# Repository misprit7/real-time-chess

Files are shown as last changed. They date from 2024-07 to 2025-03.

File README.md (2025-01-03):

<h1 align="center">
  <!--<picture><img src="./doc/img/logo.png" height="400"/></picture>-->
  <br />
  Real Time Chess
</h1>
<h2 align="center">
  A physical chess board without the concept of turns
</h2>
<h2 align="center">
  Video explanation: https://youtu.be/y7VtSK23_Jg
</h2>

# Pitch

Chess is boring. I'm boring too so I enjoy it anyways, but I can't help but think "I could design it better." Normally in chess players move sequentially in turns, but this introduces a huge latency bug that the developers of chess forgot to patch: you spend literally half the time waiting for your opponent!

The obvious solution is just get rid of the concept of turns in chess altogether and let players move whenever they want. Real time strategy games like StarCraft and Age of Empires are much more fun and spectator friendly than chess, so this should be a pretty uncontroversial minor rules update that can be implemented before the next world championship. To prevent things from getting too chaotic over the board each piece has an individual cooldown, so once it's been moved it can't move for a fixed period afterwards.

However there's an unfortunate roadblock to the widespread adoption of real time chess: as the [Niemann controversy](https://www.cnn.com/2023/09/26/sport/hans-niemann-denies-sex-toys-cheating-chess-spt-intl/index.html) has made all too clear, chess is [not immune](https://www.youtube.com/watch?v=QNuu8KTUEwU) from accusations of cheating through spectator **ass**istance or outside **anal**isys tools. Trying to have players self enforce these piece cooldowns is impossible. However where the intrinsic goodness of the human psyche fails, engineering is always ready to step in. This project is a physical chess board that keeps track and displays the cooldown remaining for each piece, and even physically holds them in place so no accidental cheating can occur.

# Design Files

The firmware and pcb kicad files are in this repo. For the physical design, see [the design on OnShape](https://cad.onshape.com/documents/ad9a4c8f8eed1cb460895551/w/e793072796f18b5ae284597f/e/b7ae406cfa566c5c0e6fed4b). Other than those parts that were cnced, here were the off the shelf components used:

- [Insulating washers](https://www.mcmaster.com/catalog/130/3683/95225A340): One under each electromagnet, to keep them isolated from the casing
- [Plastic screws](https://www.mcmaster.com/catalog/130/3446/92492A728): To attach electromagnets to base, plastic to prevent electrical connection
- [These](https://www.mcmaster.com/catalog/130/3435/92095A182) and [these](https://www.mcmaster.com/catalog/130/3435/92095A177) screws: to attach the internal supports and squares respectively
- [Spacers](https://www.mcmaster.com/catalog/94669A095): For an offset between the decorative and functional pcbs
- [Electromagnets](https://www.adafruit.com/product/3873): Most expensive part other than the machining, ~$600 per board. Could probably get them cheaper from China or something but for low quantities this was easiest

# Known Issues

- Power distribution: Traces on the pcbs are way undersized given there are many amps running through them, so there are large voltage drops when many pieces are on cooldown simultaneously. To solve this these traces should be much wider
- Tolerances: The pcbs have extremely tight tolerances which makes assmbling the board extremely annoying. The edges and holes should probably have more room
- Pin heights: The height of the pins for the banana connectors are taller than the mechanical design allows for, these are fairly easy to shorten using a dremel but probably something that should be fixed
- Corner screws: Given the order of assembly, it's impossible to insert/fasten the 4 corner screws

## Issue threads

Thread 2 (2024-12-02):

Parts list/Instructions

americoperez49, 2024-12-02:
Hey From Scratch,

Just came across your video for this. Looks super fun!

Would you be able to provide a complete parts list with links to where we could buy/manufacture the parts from?

Also a tutorial for how to build/assemble this would also be super helpful.

Thank you!

androng, 2024-12-03:
How much does one build cost?

Jannis-L, 2024-12-06:
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

A bill of materials can be found in the "releases", however the used electric magnets are not listed there. A google search resulted in all sorts of different versions that would fit the PCB design.
Additionally, there are no CAD-Files for the milled plates.

However, it seems like the project isn't ready for being copied, as the PCB is very much in a prototype state:
- screws that can short traces
- unoptimzed layout
- edges could be smaller
- not splitting the PCB in 4 parts would make it cheaper (only one controller needed) and easier to assemble. (I understand that it made sense for the first prototype)
- Having a small display with two buttons would allow for a ton of different online-only chess-variants to be played on it.
- The all-metal construction makes the project to expensive and hard to rebuild.
- In the video the board seems to be unreliable at detecting a piece being placed on a field and/or pulling it in place correctly.

The question on my mind: Is @misprit7 willing to maintain and update the project (or at least manage pull requests) to get it to a state where everyone can build their own version for a few hundred dollars or should we do a public fork and try to develop it further ourselves?

Sooly890, 2024-12-07:
Yes... please a guide would be useful

misprit7, 2024-12-08:
I added a link to the onshape mechanical files and the other parts I used in the readme. I won't be providing a guide, although I think most parts are reasonably self explanatory. If anyone does actually try to build one and runs into any issues with the files let me know any specific questions and I'd be happy to help.

As for cost, I'd probably expect at least $2500 for the first board. ~$700 for the electromagnets, ~$1000 for the cnced parts, ~$100 for the pieces, ~$300 for pcbs+components, plus a couple hundred for fasteners/materials/misc.

danaedf, 2024-12-10:
Interesting project!

If you make a new board revision, I would recommend increasing the layer count to 4 for dedicated GND/PWR layers. This should help with the voltage drops you have noticed when multiple pieces are on cooldown. Of course, you may decide against this, depending on the price, but as you mentionned in your readme, the 5V traces would need to be much larger if you keep it at 2 layers.

Also, decoupling capacitors near the electromagnets might be nice, because the in-rush current could drop the bus voltage enough to reset nearby LEDs. On the other hand, a high enough LED refresh rate might make this potential flicker unnoticeable. Adding footprints (even if you decide to not install them) for ceramic capacitors of 0.1uF for each LED and a 10uF near the eletromagnet's 5V would give you options if you notice issues.

misprit7, 2024-12-20:
@danaedf Yes you're totally right gnd/pwr planes are better for this, I remember regretting not putting them in but forgot to mention it when I wrote the last message. As for capacitors I haven't had any issues, although definitely something I was a bit worried about and would be reasonable to add.

Tomillium, 2025-02-06:
hey, could you provide a file with the pcb design.
-thanks

Tomillium, 2025-02-11:
Hey, I was wondering if the LEDs came on the pcb or not.
also if they don't which ones did you use?

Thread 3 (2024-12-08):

Improvement Suggestions

covenator, 2024-12-08:
Feature Suggestions for Improved Real-Time Chess Board Experience

1. Improved LED Lighting Appearance

Issue: The current LED lights that indicate board locations are not diffused, leading to a harsh and direct light output. Additionally, the LEDs are placed in a circular arrangement around the chess pieces but remain perfectly vertical.

Suggestions:

Add a diffusion layer or cover on top of the LEDs to soften the light, creating a cleaner and more professional appearance.

Slightly tilt the LEDs inward toward the chess piece. This ensures that the light focuses on the piece itself, enhancing visibility and aesthetics. The light will illuminate the chess piece better and make the overall look of the board more visually appealing.

---

2. Smart LED Highlighting for Legal Moves

Feature Request: Utilize the smart setup to enhance gameplay by displaying legal moves for a selected piece.

Details:

When a player picks up a chess piece, the LEDs (or an additional set of LEDs) light up to show all possible legal moves for that piece, similar to the way online chess platforms function.

Benefit: This feature makes it much easier for beginners to understand the game and reduces the learning curve, improving accessibility for all skill levels.

---

3. Visual Win Probability Display

Feature Request: Add a dynamic, visually engaging indicator that shows which player has a higher chance of winning based on the current board state.

Details:

Instead of displaying raw percentages, use a bar-style visual indicator that dynamically reflects the win probability.

The bar can be divided into two sections, each representing a player’s color. As the game progresses, the colors will expand or shrink, edging out the other player’s section based on who is currently leading.

The visual representation would resemble the win bars seen in classic fighting games like Street Fighter 2, where one color overtakes the other as the advantage shifts.

Example: If Player A is winning, their section of the bar will grow and dominate the other player's color, making the progression clear at a glance.

Benefit: This feature adds a fun and competitive element to the game, providing an intuitive and visually appealing way for players and spectators to track momentum shifts without relying on percentages alone.

Closed 2024-12-08.

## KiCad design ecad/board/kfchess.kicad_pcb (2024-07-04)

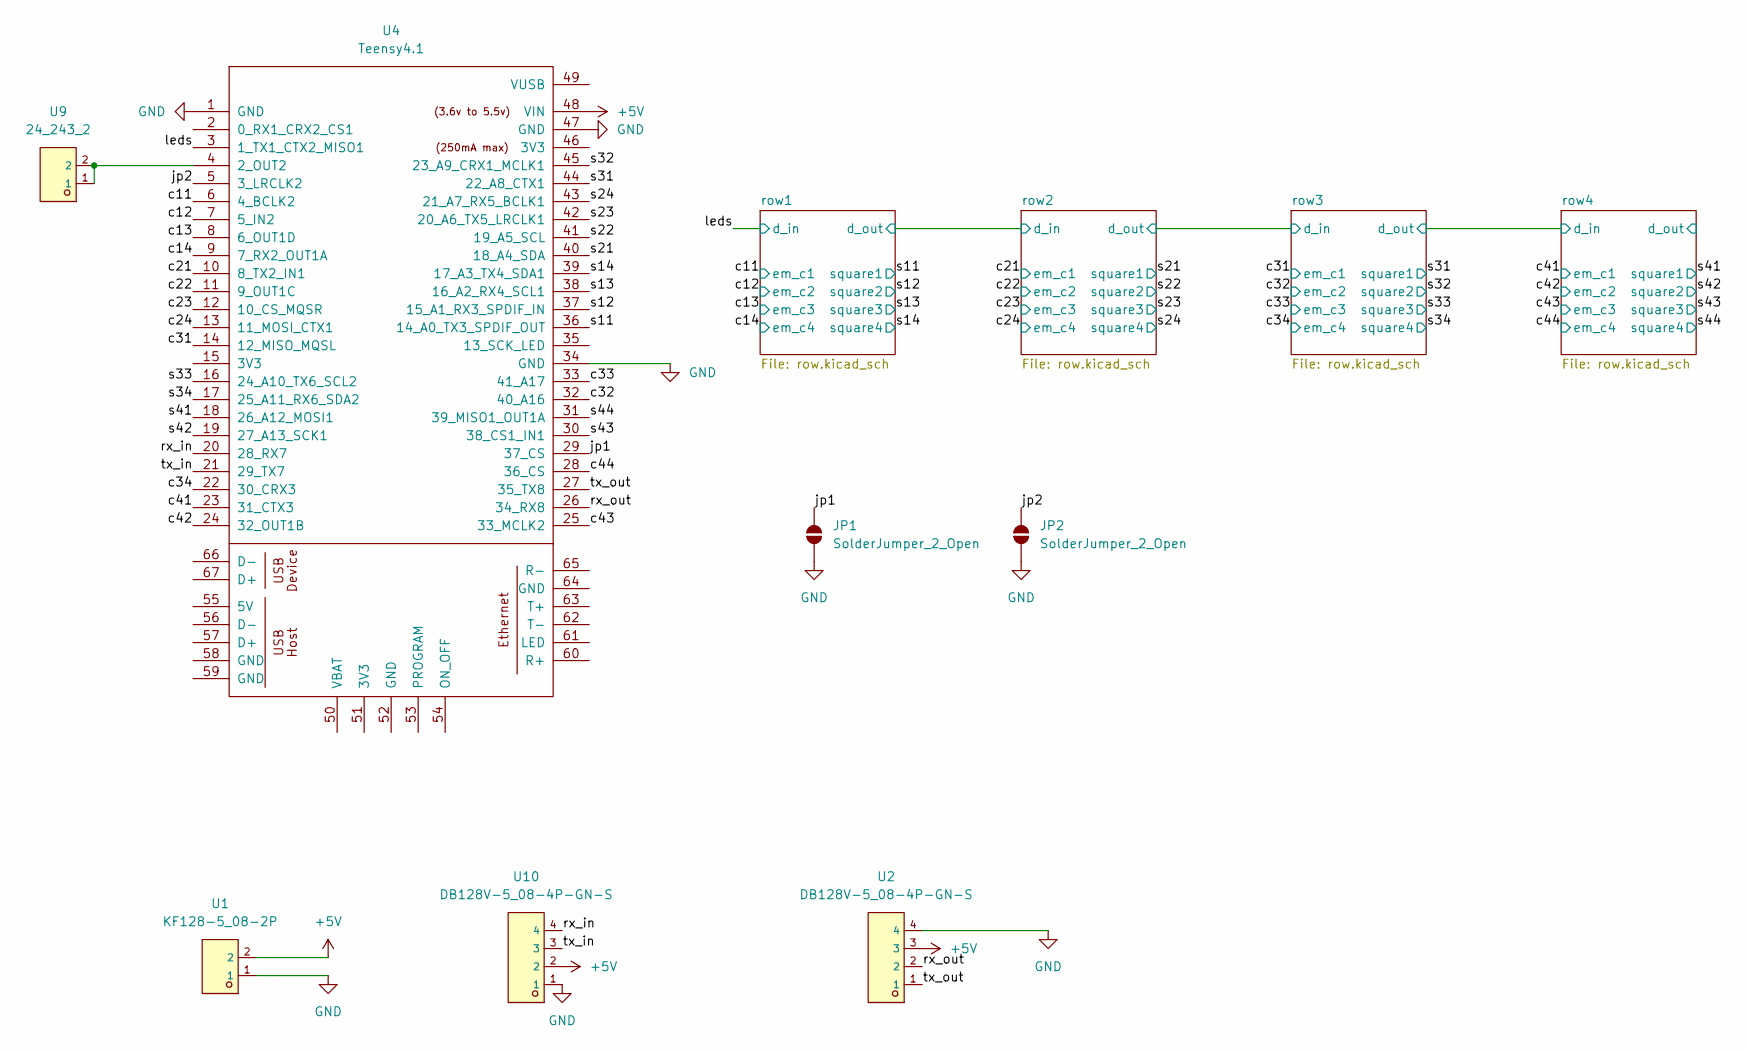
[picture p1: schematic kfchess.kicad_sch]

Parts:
JP1, JP2: SolderJumper_2_Open; SolderJumper-2_P1.3mm_Open_Pad1.0x1.5mm
U1: KF128-5_08-2P; CONN-TH_P5.08_KF128-5.08-2P; LCSC C474952
U2, U10: DB128V-5_08-4P-GN-S; CONN-TH_4P-P5.08_DIBO_DB128V-5.08; LCSC C2915641
U4: Teensy4.1; Teensy41
U9: 24_243_2; CONN-TH_24.243.2; LCSC C7437322

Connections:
+5V: U1.2, U2.3, U4.48 (VIN), U10.2; also elsewhere on the board
/c11: U4.6 (4_BCLK2); also elsewhere on the board
/c12: U4.7 (5_IN2); also elsewhere on the board
/c13: U4.8 (6_OUT1D); also elsewhere on the board
/c14: U4.9 (7_RX2_OUT1A); also elsewhere on the board
/c21: U4.10 (8_TX2_IN1); also elsewhere on the board
/c22: U4.11 (9_OUT1C); also elsewhere on the board
/c23: U4.12 (10_CS_MQSR); also elsewhere on the board
/c24: U4.13 (11_MOSI_CTX1); also elsewhere on the board
/c31: U4.14 (12_MISO_MQSL); also elsewhere on the board
/c32: U4.32 (40_A16); also elsewhere on the board
/c33: U4.33 (41_A17); also elsewhere on the board
/c34: U4.22 (30_CRX3); also elsewhere on the board
/c41: U4.23 (31_CTX3); also elsewhere on the board
/c42: U4.24 (32_OUT1B); also elsewhere on the board
/c43: U4.25 (33_MCLK2); also elsewhere on the board
/c44: U4.28 (36_CS); also elsewhere on the board
/jp1: JP1.2 (B), U4.29 (37_CS)
/jp2: JP2.2 (B), U4.5 (3_LRCLK2)
/leds: U4.3 (1_TX1_CTX2_MISO1); also elsewhere on the board
/rx_in: U4.20 (28_RX7), U10.4
/rx_out: U2.2, U4.26 (34_RX8)
/s11: U4.36 (14_A0_TX3_SPDIF_OUT); also elsewhere on the board
/s12: U4.37 (15_A1_RX3_SPDIF_IN); also elsewhere on the board
/s13: U4.38 (16_A2_RX4_SCL1); also elsewhere on the board
/s14: U4.39 (17_A3_TX4_SDA1); also elsewhere on the board
/s21: U4.40 (18_A4_SDA); also elsewhere on the board
/s22: U4.41 (19_A5_SCL); also elsewhere on the board
/s23: U4.42 (20_A6_TX5_LRCLK1); also elsewhere on the board
/s24: U4.43 (21_A7_RX5_BCLK1); also elsewhere on the board
/s31: U4.44 (22_A8_CTX1); also elsewhere on the board
/s32: U4.45 (23_A9_CRX1_MCLK1); also elsewhere on the board
/s33: U4.16 (24_A10_TX6_SCL2); also elsewhere on the board
/s34: U4.17 (25_A11_RX6_SDA2); also elsewhere on the board
/s41: U4.18 (26_A12_MOSI1); also elsewhere on the board
/s42: U4.19 (27_A13_SCK1); also elsewhere on the board
/s43: U4.30 (38_CS1_IN1); also elsewhere on the board
/s44: U4.31 (39_MISO1_OUT1A); also elsewhere on the board
/tx_in: U4.21 (29_TX7), U10.3
/tx_out: U2.1, U4.27 (35_TX8)
GND: JP1.1 (A), JP2.1 (A), U1.1, U2.4, U4.1 (GND), U4.34 (GND), U4.47 (GND), U10.1; also elsewhere on the board
unnamed: U4.4 (2_OUT2), U9.1, U9.2

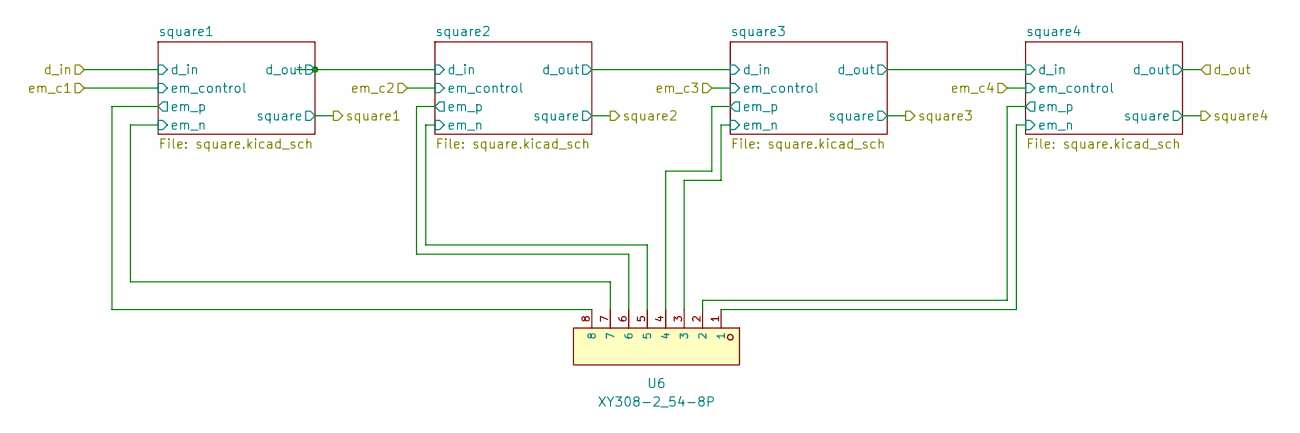
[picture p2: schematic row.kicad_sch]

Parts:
U6: XY308-2_54-8P; CONN-TH_XY308-2.54-8P; LCSC C915917

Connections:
+5V: U6.2, U6.4, U6.6, U6.8; also elsewhere on the board
/row2/square1/em_n: U6.7; also elsewhere on the board
/row2/square2/em_n: U6.5; also elsewhere on the board
/row2/square3/em_n: U6.3; also elsewhere on the board
/row2/square4/em_n: U6.1; also elsewhere on the board

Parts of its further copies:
U5, U7, U8: XY308-2_54-8P; CONN-TH_XY308-2.54-8P; LCSC C915917

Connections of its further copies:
+5V: U5.2, U5.4, U5.6, U5.8, U7.2, U7.4, U7.6, U7.8, U8.2, U8.4, U8.6, U8.8; also elsewhere on the board
/row1/square1/em_n: U5.7; also elsewhere on the board
/row1/square2/em_n: U5.5; also elsewhere on the board
/row1/square3/em_n: U5.3; also elsewhere on the board
/row1/square4/em_n: U5.1; also elsewhere on the board
/row3/square1/em_n: U7.7; also elsewhere on the board
/row3/square2/em_n: U7.5; also elsewhere on the board
/row3/square3/em_n: U7.3; also elsewhere on the board
/row3/square4/em_n: U7.1; also elsewhere on the board
/row4/square1/em_n: U8.7; also elsewhere on the board
/row4/square2/em_n: U8.5; also elsewhere on the board
/row4/square3/em_n: U8.3; also elsewhere on the board
/row4/square4/em_n: U8.1; also elsewhere on the board

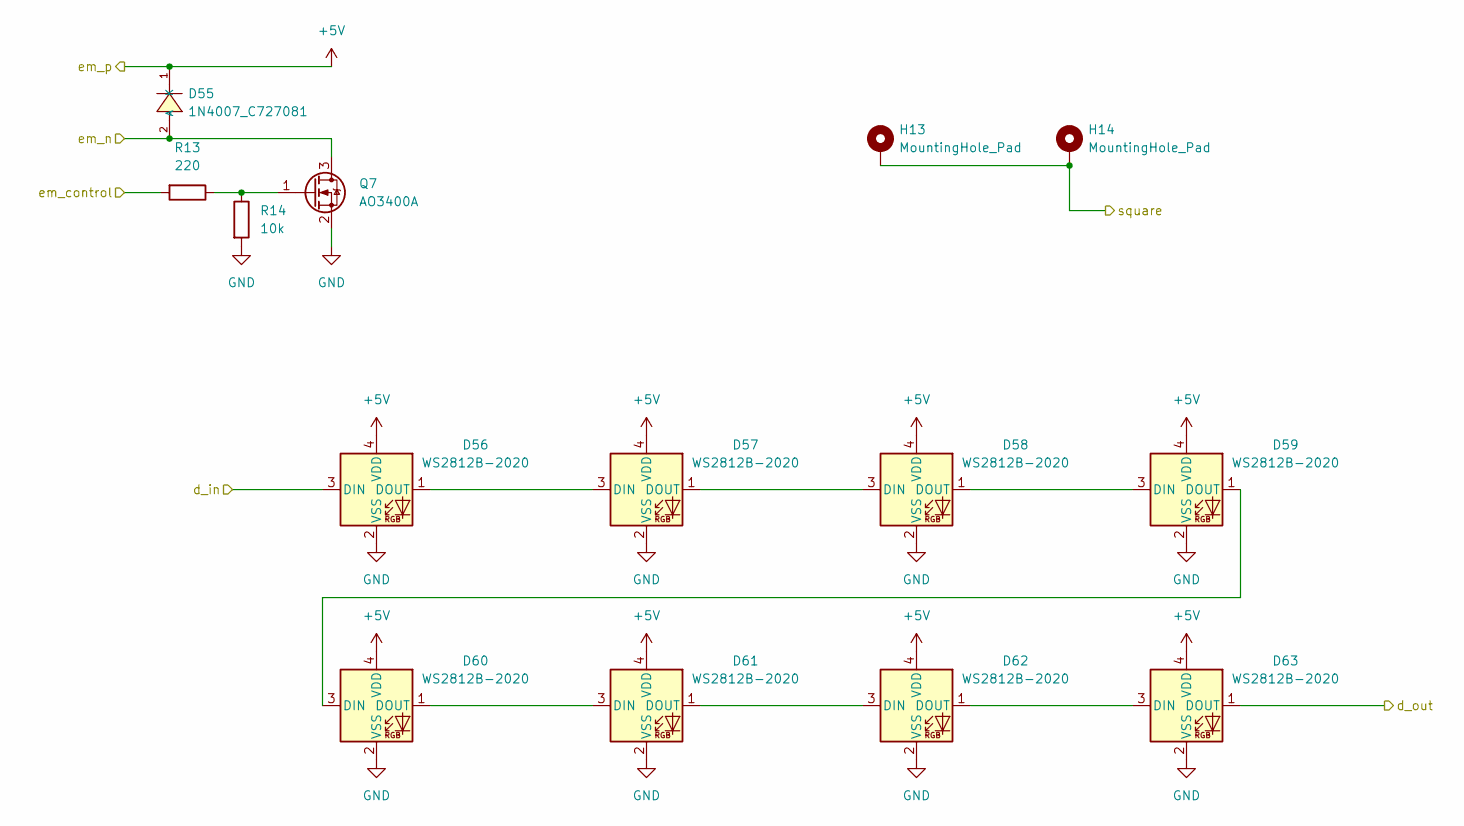
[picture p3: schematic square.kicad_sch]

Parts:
D55: 1N4007_C727081; SMA_L4.3-W2.5-LS5.0-RD; LCSC C727081
D56, D57, D58, D59, D60, D61, D62, D63: WS2812B-2020; LED_WS2812B-2020_PLCC4_2.0x2.0mm
H13, H14: MountingHole_Pad; MountingHole_3.2mm_M3_Pad
Q7: AO3400A; SOT-23
R13: 220; R_0603_1608Metric
R14: 10k; R_0603_1608Metric

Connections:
+5V: D55.1 (K), D56.4 (VDD), D57.4 (VDD), D58.4 (VDD), D59.4 (VDD), D60.4 (VDD), D61.4 (VDD), D62.4 (VDD), D63.4 (VDD); also elsewhere on the board
/c23: R13.2; also elsewhere on the board
/row2/square2/d_out: D56.3 (DIN); also elsewhere on the board
/row2/square3/d_out: D63.1 (DOUT); also elsewhere on the board
/row2/square3/em_n: D55.2 (A), Q7.3 (D); also elsewhere on the board
/s23: H13.1, H14.1; also elsewhere on the board
GND: D56.2 (VSS), D57.2 (VSS), D58.2 (VSS), D59.2 (VSS), D60.2 (VSS), D61.2 (VSS), D62.2 (VSS), D63.2 (VSS), Q7.2 (S), R14.2; also elsewhere on the board
unnamed: D56.1 (DOUT), D57.3 (DIN)
unnamed: D57.1 (DOUT), D58.3 (DIN)
unnamed: D58.1 (DOUT), D59.3 (DIN)
unnamed: D59.1 (DOUT), D60.3 (DIN)
unnamed: D60.1 (DOUT), D61.3 (DIN)
unnamed: D61.1 (DOUT), D62.3 (DIN)
unnamed: D62.1 (DOUT), D63.3 (DIN)
unnamed: Q7.1 (G), R13.1, R14.1

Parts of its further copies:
D1, D10, D19, D28, D37, D46, D64, D73, D82, D91, D100, D109, D118, D127, D136: 1N4007_C727081; SMA_L4.3-W2.5-LS5.0-RD; LCSC C727081
D2, D3, D4, D5, D6, D7, D8, D9, D11, D12, D13, D14, D15, D16, D17, D18, D20, D21, D22, D23, D24, D25, D26, D27, D29, D30, D31, D32, D33, D34, D35, D36, D38, D39, D40, D41, D42, D43, D44, D45, D47, D48, D49, D50, D51, D52, D53, D54, D65, D66, D67, D68, D69, D70, D71, D72, D74, D75, D76, D77, D78, D79, D80, D81, D83, D84, D85, D86, D87, D88, D89, D90, D92, D93, D94, D95, D96, D97, D98, D99, D101, D102, D103, D104, D105, D106, D107, D108, D110, D111, D112, D113, D114, D115, D116, D117, D119, D120, D121, D122, D123, D124, D125, D126, D128, D129, D130, D131, D132, D133, D134, D135, D137, D138, D139, D140, D141, D142, D143, D144: WS2812B-2020; LED_WS2812B-2020_PLCC4_2.0x2.0mm
H1, H2, H3, H4, H5, H6, H7, H8, H9, H10, H11, H12, H15, H16, H17, H18, H19, H20, H21, H22, H23, H24, H25, H26, H27, H28, H29, H30, H31, H32: MountingHole_Pad; MountingHole_3.2mm_M3_Pad
Q1, Q2, Q3, Q4, Q5, Q6, Q8, Q9, Q10, Q11, Q12, Q13, Q14, Q15, Q16: AO3400A; SOT-23
R1, R3, R5, R7, R9, R11, R15, R17, R19, R21, R23, R25, R27, R29, R31: 220; R_0603_1608Metric
R2, R4, R6, R8, R10, R12, R16, R18, R20, R22, R24, R26, R28, R30, R32: 10k; R_0603_1608Metric

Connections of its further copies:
+5V: D1.1 (K), D2.4 (VDD), D3.4 (VDD), D4.4 (VDD), D5.4 (VDD), D6.4 (VDD), D7.4 (VDD), D8.4 (VDD), D9.4 (VDD), D10.1 (K), D11.4 (VDD), D12.4 (VDD), D13.4 (VDD), D14.4 (VDD), D15.4 (VDD), D16.4 (VDD), D17.4 (VDD), D18.4 (VDD), D19.1 (K), D20.4 (VDD), D21.4 (VDD), D22.4 (VDD), D23.4 (VDD), D24.4 (VDD), D25.4 (VDD), D26.4 (VDD), D27.4 (VDD), D28.1 (K), D29.4 (VDD), D30.4 (VDD), D31.4 (VDD), D32.4 (VDD), D33.4 (VDD), D34.4 (VDD), D35.4 (VDD), D36.4 (VDD), D37.1 (K), D38.4 (VDD), D39.4 (VDD), D40.4 (VDD), D41.4 (VDD), D42.4 (VDD), D43.4 (VDD), D44.4 (VDD), D45.4 (VDD), D46.1 (K), D47.4 (VDD), D48.4 (VDD), D49.4 (VDD), D50.4 (VDD), D51.4 (VDD), D52.4 (VDD), D53.4 (VDD), D54.4 (VDD), D64.1 (K), D65.4 (VDD), D66.4 (VDD), D67.4 (VDD), D68.4 (VDD), D69.4 (VDD), D70.4 (VDD), D71.4 (VDD), D72.4 (VDD), D73.1 (K), D74.4 (VDD), D75.4 (VDD), D76.4 (VDD), D77.4 (VDD), D78.4 (VDD), D79.4 (VDD), D80.4 (VDD), D81.4 (VDD), D82.1 (K), D83.4 (VDD), D84.4 (VDD), D85.4 (VDD), D86.4 (VDD), D87.4 (VDD), D88.4 (VDD), D89.4 (VDD), D90.4 (VDD), D91.1 (K), D92.4 (VDD), D93.4 (VDD), D94.4 (VDD), D95.4 (VDD), D96.4 (VDD), D97.4 (VDD), D98.4 (VDD), D99.4 (VDD), D100.1 (K), D101.4 (VDD), D102.4 (VDD), D103.4 (VDD), D104.4 (VDD), D105.4 (VDD), D106.4 (VDD), D107.4 (VDD), D108.4 (VDD), D109.1 (K), D110.4 (VDD), D111.4 (VDD), D112.4 (VDD), D113.4 (VDD), D114.4 (VDD), D115.4 (VDD), D116.4 (VDD), D117.4 (VDD), D118.1 (K), D119.4 (VDD), D120.4 (VDD), D121.4 (VDD), D122.4 (VDD), D123.4 (VDD), D124.4 (VDD), D125.4 (VDD), D126.4 (VDD), D127.1 (K), D128.4 (VDD), D129.4 (VDD), D130.4 (VDD), D131.4 (VDD), D132.4 (VDD), D133.4 (VDD), D134.4 (VDD), D135.4 (VDD), D136.1 (K), D137.4 (VDD), D138.4 (VDD), D139.4 (VDD), D140.4 (VDD), D141.4 (VDD), D142.4 (VDD), D143.4 (VDD), D144.4 (VDD); also elsewhere on the board
/c11: R1.2; also elsewhere on the board
/c12: R3.2; also elsewhere on the board
/c13: R5.2; also elsewhere on the board
/c14: R7.2; also elsewhere on the board
/c21: R9.2; also elsewhere on the board
/c22: R11.2; also elsewhere on the board
/c24: R15.2; also elsewhere on the board
/c31: R17.2; also elsewhere on the board
/c32: R19.2; also elsewhere on the board
/c33: R21.2; also elsewhere on the board
/c34: R23.2; also elsewhere on the board
/c41: R25.2; also elsewhere on the board
/c42: R27.2; also elsewhere on the board
/c43: R29.2; also elsewhere on the board
/c44: R31.2; also elsewhere on the board
/leds: D2.3 (DIN); also elsewhere on the board
/row1/d_out: D36.1 (DOUT), D38.3 (DIN)
/row1/square1/d_out: D9.1 (DOUT), D11.3 (DIN)
/row1/square1/em_n: D1.2 (A), Q1.3 (D); also elsewhere on the board
/row1/square2/d_out: D18.1 (DOUT), D20.3 (DIN)
/row1/square2/em_n: D10.2 (A), Q2.3 (D); also elsewhere on the board
/row1/square3/d_out: D27.1 (DOUT), D29.3 (DIN)
/row1/square3/em_n: D19.2 (A), Q3.3 (D); also elsewhere on the board
/row1/square4/em_n: D28.2 (A), Q4.3 (D); also elsewhere on the board
/row2/d_out: D72.1 (DOUT), D74.3 (DIN)
/row2/square1/d_out: D45.1 (DOUT), D47.3 (DIN)
/row2/square1/em_n: D37.2 (A), Q5.3 (D); also elsewhere on the board
/row2/square2/d_out: D54.1 (DOUT); also elsewhere on the board
/row2/square2/em_n: D46.2 (A), Q6.3 (D); also elsewhere on the board
/row2/square3/d_out: D65.3 (DIN); also elsewhere on the board
/row2/square4/em_n: D64.2 (A), Q8.3 (D); also elsewhere on the board
/row3/d_out: D108.1 (DOUT), D110.3 (DIN)
/row3/square1/d_out: D81.1 (DOUT), D83.3 (DIN)
/row3/square1/em_n: D73.2 (A), Q9.3 (D); also elsewhere on the board
/row3/square2/d_out: D90.1 (DOUT), D92.3 (DIN)
/row3/square2/em_n: D82.2 (A), Q10.3 (D); also elsewhere on the board
/row3/square3/d_out: D99.1 (DOUT), D101.3 (DIN)
/row3/square3/em_n: D91.2 (A), Q11.3 (D); also elsewhere on the board
/row3/square4/em_n: D100.2 (A), Q12.3 (D); also elsewhere on the board
/row4/d_out: D144.1 (DOUT)
/row4/square1/d_out: D117.1 (DOUT), D119.3 (DIN)
/row4/square1/em_n: D109.2 (A), Q13.3 (D); also elsewhere on the board
/row4/square2/d_out: D126.1 (DOUT), D128.3 (DIN)
/row4/square2/em_n: D118.2 (A), Q14.3 (D); also elsewhere on the board
/row4/square3/d_out: D135.1 (DOUT), D137.3 (DIN)
/row4/square3/em_n: D127.2 (A), Q15.3 (D); also elsewhere on the board
/row4/square4/em_n: D136.2 (A), Q16.3 (D); also elsewhere on the board
/s11: H1.1, H2.1; also elsewhere on the board
/s12: H3.1, H4.1; also elsewhere on the board
/s13: H5.1, H6.1; also elsewhere on the board
/s14: H7.1, H8.1; also elsewhere on the board
/s21: H9.1, H10.1; also elsewhere on the board
/s22: H11.1, H12.1; also elsewhere on the board
/s24: H15.1, H16.1; also elsewhere on the board
/s31: H17.1, H18.1; also elsewhere on the board
/s32: H19.1, H20.1; also elsewhere on the board
/s33: H21.1, H22.1; also elsewhere on the board
/s34: H23.1, H24.1; also elsewhere on the board
/s41: H25.1, H26.1; also elsewhere on the board
/s42: H27.1, H28.1; also elsewhere on the board
/s43: H29.1, H30.1; also elsewhere on the board
/s44: H31.1, H32.1; also elsewhere on the board
GND: D2.2 (VSS), D3.2 (VSS), D4.2 (VSS), D5.2 (VSS), D6.2 (VSS), D7.2 (VSS), D8.2 (VSS), D9.2 (VSS), D11.2 (VSS), D12.2 (VSS), D13.2 (VSS), D14.2 (VSS), D15.2 (VSS), D16.2 (VSS), D17.2 (VSS), D18.2 (VSS), D20.2 (VSS), D21.2 (VSS), D22.2 (VSS), D23.2 (VSS), D24.2 (VSS), D25.2 (VSS), D26.2 (VSS), D27.2 (VSS), D29.2 (VSS), D30.2 (VSS), D31.2 (VSS), D32.2 (VSS), D33.2 (VSS), D34.2 (VSS), D35.2 (VSS), D36.2 (VSS), D38.2 (VSS), D39.2 (VSS), D40.2 (VSS), D41.2 (VSS), D42.2 (VSS), D43.2 (VSS), D44.2 (VSS), D45.2 (VSS), D47.2 (VSS), D48.2 (VSS), D49.2 (VSS), D50.2 (VSS), D51.2 (VSS), D52.2 (VSS), D53.2 (VSS), D54.2 (VSS), D65.2 (VSS), D66.2 (VSS), D67.2 (VSS), D68.2 (VSS), D69.2 (VSS), D70.2 (VSS), D71.2 (VSS), D72.2 (VSS), D74.2 (VSS), D75.2 (VSS), D76.2 (VSS), D77.2 (VSS), D78.2 (VSS), D79.2 (VSS), D80.2 (VSS), D81.2 (VSS), D83.2 (VSS), D84.2 (VSS), D85.2 (VSS), D86.2 (VSS), D87.2 (VSS), D88.2 (VSS), D89.2 (VSS), D90.2 (VSS), D92.2 (VSS), D93.2 (VSS), D94.2 (VSS), D95.2 (VSS), D96.2 (VSS), D97.2 (VSS), D98.2 (VSS), D99.2 (VSS), D101.2 (VSS), D102.2 (VSS), D103.2 (VSS), D104.2 (VSS), D105.2 (VSS), D106.2 (VSS), D107.2 (VSS), D108.2 (VSS), D110.2 (VSS), D111.2 (VSS), D112.2 (VSS), D113.2 (VSS), D114.2 (VSS), D115.2 (VSS), D116.2 (VSS), D117.2 (VSS), D119.2 (VSS), D120.2 (VSS), D121.2 (VSS), D122.2 (VSS), D123.2 (VSS), D124.2 (VSS), D125.2 (VSS), D126.2 (VSS), D128.2 (VSS), D129.2 (VSS), D130.2 (VSS), D131.2 (VSS), D132.2 (VSS), D133.2 (VSS), D134.2 (VSS), D135.2 (VSS), D137.2 (VSS), D138.2 (VSS), D139.2 (VSS), D140.2 (VSS), D141.2 (VSS), D142.2 (VSS), D143.2 (VSS), D144.2 (VSS), Q1.2 (S), Q2.2 (S), Q3.2 (S), Q4.2 (S), Q5.2 (S), Q6.2 (S), Q8.2 (S), Q9.2 (S), Q10.2 (S), Q11.2 (S), Q12.2 (S), Q13.2 (S), Q14.2 (S), Q15.2 (S), Q16.2 (S), R2.2, R4.2, R6.2, R8.2, R10.2, R12.2, R16.2, R18.2, R20.2, R22.2, R24.2, R26.2, R28.2, R30.2, R32.2; also elsewhere on the board
unnamed: D2.1 (DOUT), D3.3 (DIN)
unnamed: D3.1 (DOUT), D4.3 (DIN)
unnamed: D4.1 (DOUT), D5.3 (DIN)
unnamed: D5.1 (DOUT), D6.3 (DIN)
unnamed: D6.1 (DOUT), D7.3 (DIN)
unnamed: D7.1 (DOUT), D8.3 (DIN)
unnamed: D8.1 (DOUT), D9.3 (DIN)
unnamed: D11.1 (DOUT), D12.3 (DIN)
unnamed: D12.1 (DOUT), D13.3 (DIN)
unnamed: D13.1 (DOUT), D14.3 (DIN)
unnamed: D14.1 (DOUT), D15.3 (DIN)
unnamed: D15.1 (DOUT), D16.3 (DIN)
unnamed: D16.1 (DOUT), D17.3 (DIN)
unnamed: D17.1 (DOUT), D18.3 (DIN)
unnamed: D20.1 (DOUT), D21.3 (DIN)
unnamed: D21.1 (DOUT), D22.3 (DIN)
unnamed: D22.1 (DOUT), D23.3 (DIN)
unnamed: D23.1 (DOUT), D24.3 (DIN)
unnamed: D24.1 (DOUT), D25.3 (DIN)
unnamed: D25.1 (DOUT), D26.3 (DIN)
unnamed: D26.1 (DOUT), D27.3 (DIN)
unnamed: D29.1 (DOUT), D30.3 (DIN)
unnamed: D30.1 (DOUT), D31.3 (DIN)
unnamed: D31.1 (DOUT), D32.3 (DIN)
unnamed: D32.1 (DOUT), D33.3 (DIN)
unnamed: D33.1 (DOUT), D34.3 (DIN)
unnamed: D34.1 (DOUT), D35.3 (DIN)
unnamed: D35.1 (DOUT), D36.3 (DIN)
unnamed: D38.1 (DOUT), D39.3 (DIN)
unnamed: D39.1 (DOUT), D40.3 (DIN)
unnamed: D40.1 (DOUT), D41.3 (DIN)
unnamed: D41.1 (DOUT), D42.3 (DIN)
unnamed: D42.1 (DOUT), D43.3 (DIN)
unnamed: D43.1 (DOUT), D44.3 (DIN)
unnamed: D44.1 (DOUT), D45.3 (DIN)
unnamed: D47.1 (DOUT), D48.3 (DIN)
unnamed: D48.1 (DOUT), D49.3 (DIN)
unnamed: D49.1 (DOUT), D50.3 (DIN)
unnamed: D50.1 (DOUT), D51.3 (DIN)
unnamed: D51.1 (DOUT), D52.3 (DIN)
unnamed: D52.1 (DOUT), D53.3 (DIN)
unnamed: D53.1 (DOUT), D54.3 (DIN)
unnamed: D65.1 (DOUT), D66.3 (DIN)
unnamed: D66.1 (DOUT), D67.3 (DIN)
unnamed: D67.1 (DOUT), D68.3 (DIN)
unnamed: D68.1 (DOUT), D69.3 (DIN)
unnamed: D69.1 (DOUT), D70.3 (DIN)
unnamed: D70.1 (DOUT), D71.3 (DIN)
unnamed: D71.1 (DOUT), D72.3 (DIN)
unnamed: D74.1 (DOUT), D75.3 (DIN)
unnamed: D75.1 (DOUT), D76.3 (DIN)
unnamed: D76.1 (DOUT), D77.3 (DIN)
unnamed: D77.1 (DOUT), D78.3 (DIN)
unnamed: D78.1 (DOUT), D79.3 (DIN)
unnamed: D79.1 (DOUT), D80.3 (DIN)
unnamed: D80.1 (DOUT), D81.3 (DIN)
unnamed: D83.1 (DOUT), D84.3 (DIN)
unnamed: D84.1 (DOUT), D85.3 (DIN)
unnamed: D85.1 (DOUT), D86.3 (DIN)
unnamed: D86.1 (DOUT), D87.3 (DIN)
unnamed: D87.1 (DOUT), D88.3 (DIN)
unnamed: D88.1 (DOUT), D89.3 (DIN)
unnamed: D89.1 (DOUT), D90.3 (DIN)
unnamed: D92.1 (DOUT), D93.3 (DIN)
unnamed: D93.1 (DOUT), D94.3 (DIN)
unnamed: D94.1 (DOUT), D95.3 (DIN)
unnamed: D95.1 (DOUT), D96.3 (DIN)
unnamed: D96.1 (DOUT), D97.3 (DIN)
unnamed: D97.1 (DOUT), D98.3 (DIN)
unnamed: D98.1 (DOUT), D99.3 (DIN)
unnamed: D101.1 (DOUT), D102.3 (DIN)
unnamed: D102.1 (DOUT), D103.3 (DIN)
unnamed: D103.1 (DOUT), D104.3 (DIN)
unnamed: D104.1 (DOUT), D105.3 (DIN)
unnamed: D105.1 (DOUT), D106.3 (DIN)
unnamed: D106.1 (DOUT), D107.3 (DIN)
unnamed: D107.1 (DOUT), D108.3 (DIN)
unnamed: D110.1 (DOUT), D111.3 (DIN)
unnamed: D111.1 (DOUT), D112.3 (DIN)
unnamed: D112.1 (DOUT), D113.3 (DIN)
unnamed: D113.1 (DOUT), D114.3 (DIN)
unnamed: D114.1 (DOUT), D115.3 (DIN)
unnamed: D115.1 (DOUT), D116.3 (DIN)
unnamed: D116.1 (DOUT), D117.3 (DIN)
unnamed: D119.1 (DOUT), D120.3 (DIN)
unnamed: D120.1 (DOUT), D121.3 (DIN)
unnamed: D121.1 (DOUT), D122.3 (DIN)
unnamed: D122.1 (DOUT), D123.3 (DIN)
unnamed: D123.1 (DOUT), D124.3 (DIN)
unnamed: D124.1 (DOUT), D125.3 (DIN)
unnamed: D125.1 (DOUT), D126.3 (DIN)
unnamed: D128.1 (DOUT), D129.3 (DIN)
unnamed: D129.1 (DOUT), D130.3 (DIN)
unnamed: D130.1 (DOUT), D131.3 (DIN)
unnamed: D131.1 (DOUT), D132.3 (DIN)
unnamed: D132.1 (DOUT), D133.3 (DIN)
unnamed: D133.1 (DOUT), D134.3 (DIN)
unnamed: D134.1 (DOUT), D135.3 (DIN)
unnamed: D137.1 (DOUT), D138.3 (DIN)
unnamed: D138.1 (DOUT), D139.3 (DIN)
unnamed: D139.1 (DOUT), D140.3 (DIN)
unnamed: D140.1 (DOUT), D141.3 (DIN)
unnamed: D141.1 (DOUT), D142.3 (DIN)
unnamed: D142.1 (DOUT), D143.3 (DIN)
unnamed: D143.1 (DOUT), D144.3 (DIN)
unnamed: Q1.1 (G), R1.1, R2.1
unnamed: Q2.1 (G), R3.1, R4.1
unnamed: Q3.1 (G), R5.1, R6.1
unnamed: Q4.1 (G), R7.1, R8.1
unnamed: Q5.1 (G), R9.1, R10.1
unnamed: Q6.1 (G), R11.1, R12.1
unnamed: Q8.1 (G), R15.1, R16.1
unnamed: Q9.1 (G), R17.1, R18.1
unnamed: Q10.1 (G), R19.1, R20.1
unnamed: Q11.1 (G), R21.1, R22.1
unnamed: Q12.1 (G), R23.1, R24.1
unnamed: Q13.1 (G), R25.1, R26.1
unnamed: Q14.1 (G), R27.1, R28.1
unnamed: Q15.1 (G), R29.1, R30.1
unnamed: Q16.1 (G), R31.1, R32.1

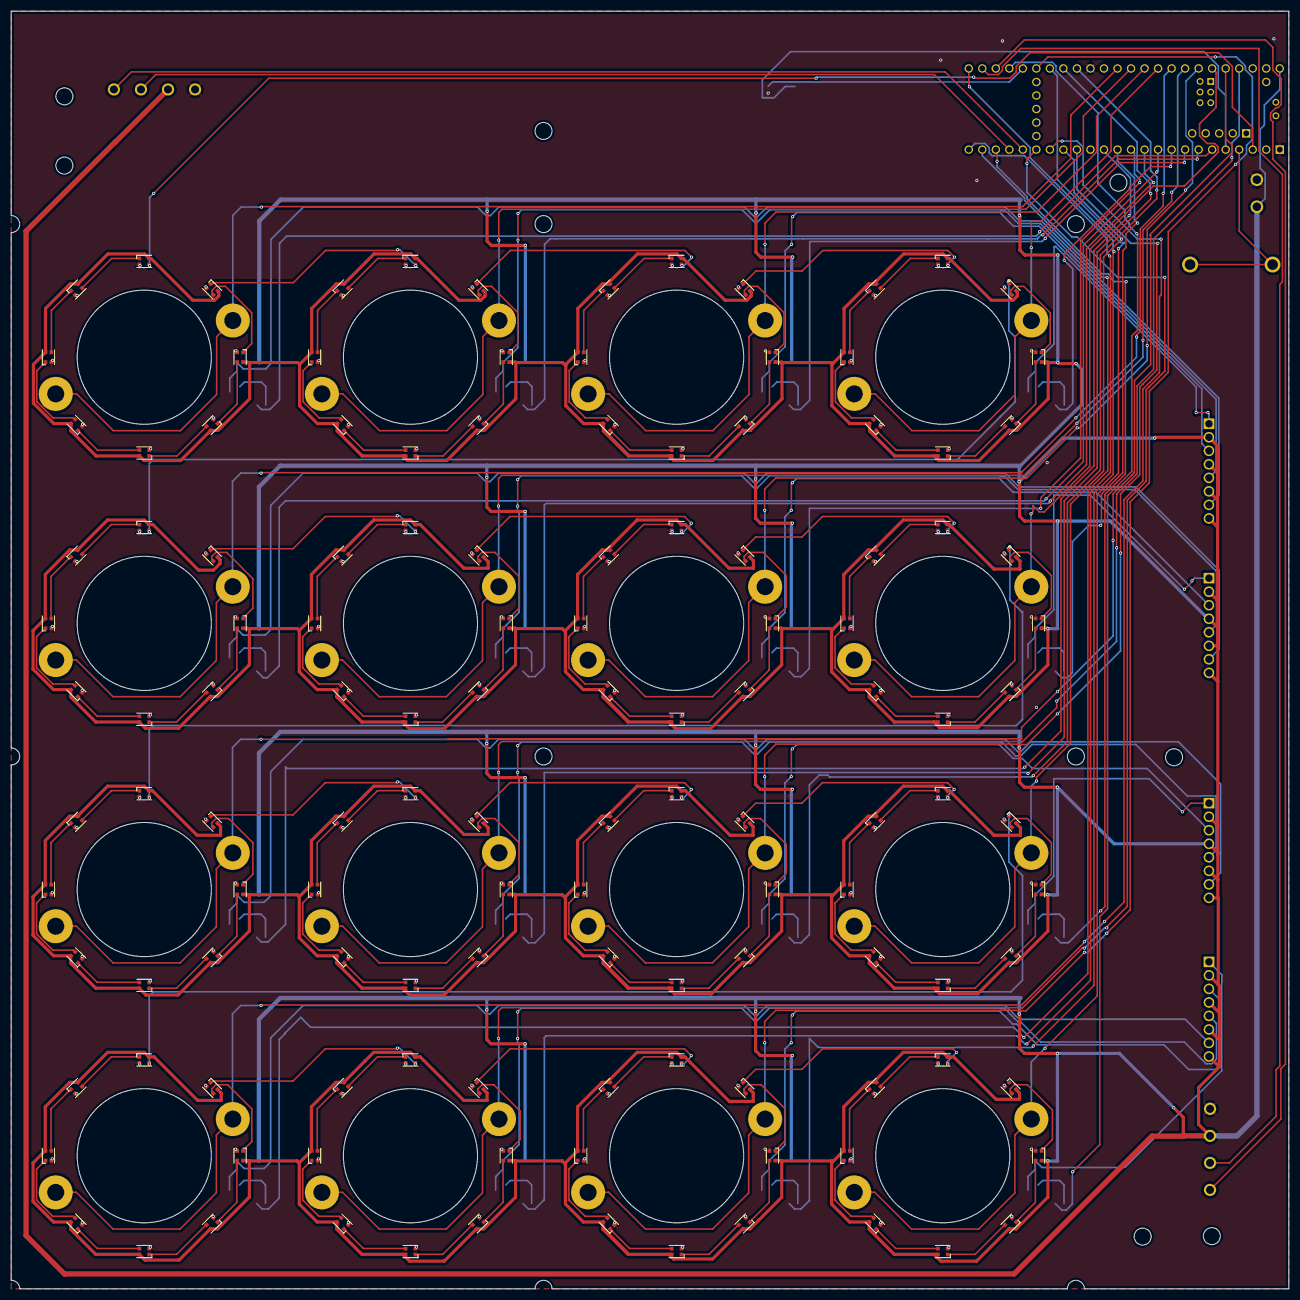
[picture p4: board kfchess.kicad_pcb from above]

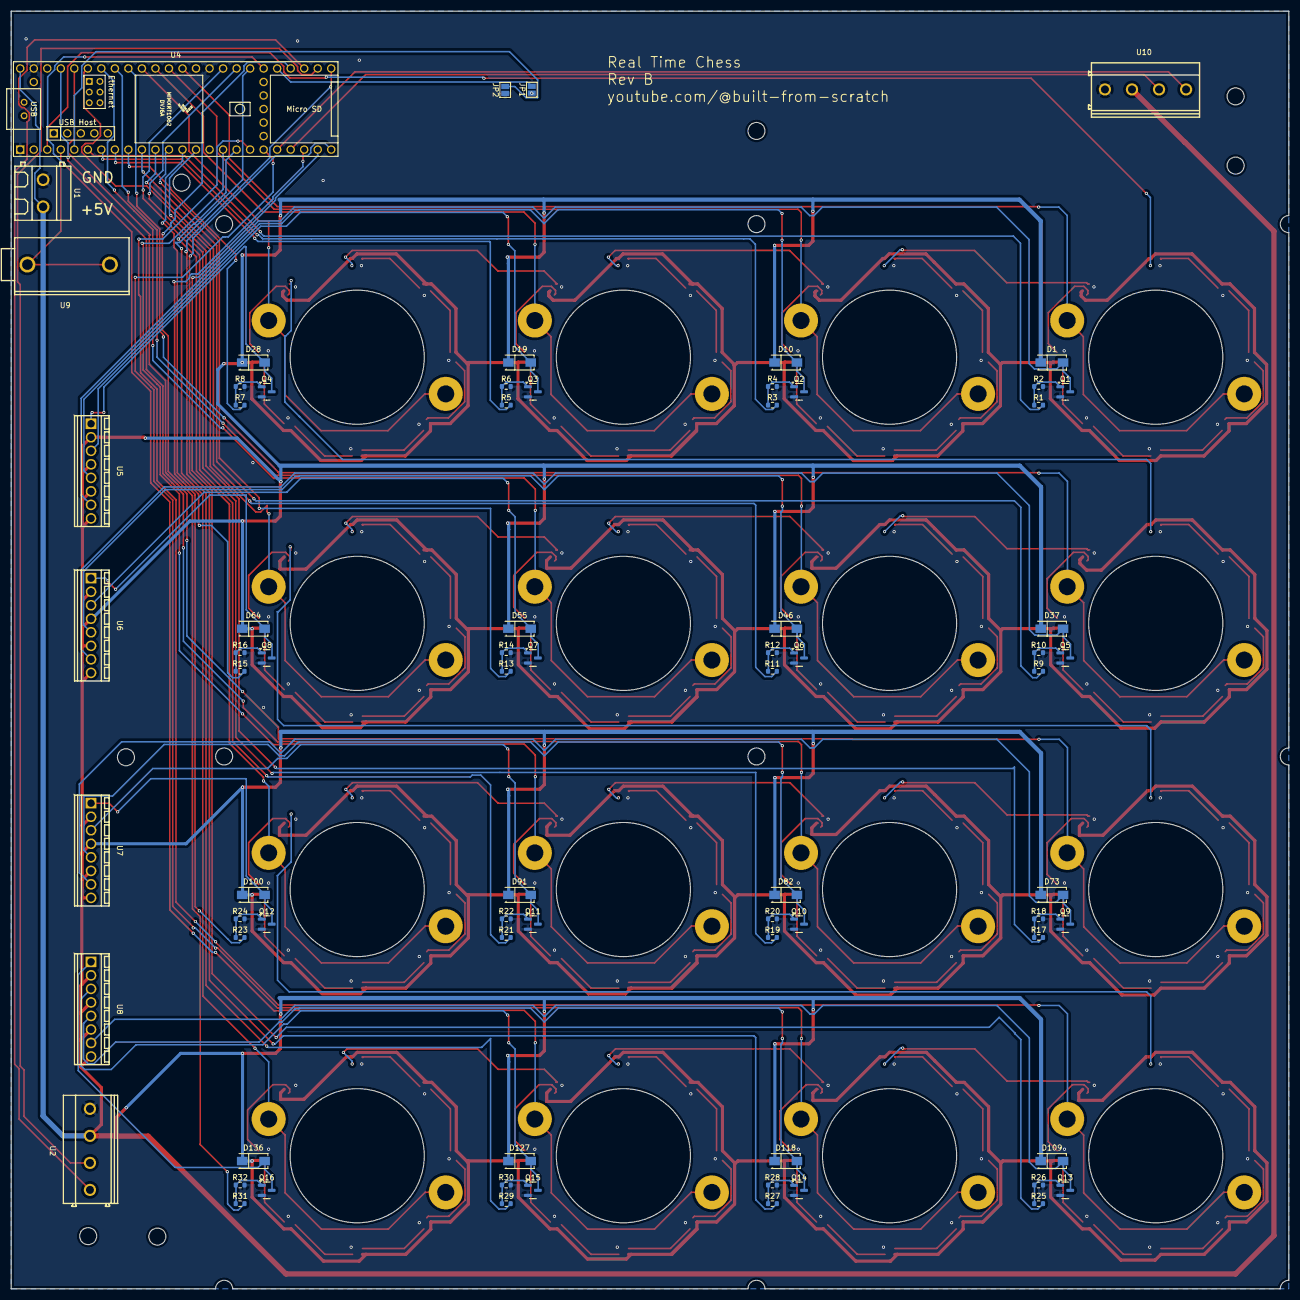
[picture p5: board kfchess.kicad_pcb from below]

Board: 2 copper layers, 240.0 x 240.0 mm, 235 parts (75 on the bottom side), 201 nets.

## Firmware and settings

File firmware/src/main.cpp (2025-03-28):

// There are two speedup options for some of the FFT code:

// Define this to use reciprocal multiplication for division and some more speedups that might decrease precision
//#define FFT_SPEED_OVER_PRECISION

// Define this to use a low-precision square root approximation instead of the regular sqrt() call
// This might only work for specific use cases, but is significantly faster. Only works for ArduinoFFT<float>.
//#define FFT_SQRT_APPROXIMATION

/******************************************************************************
 * Includes
 ******************************************************************************/

// Overrides default arduino_freertos config
// Pretty sure I didn't do this right, but no 
/*#include "freeRTOSConfig.h"*/

#include "arduino_freertos.h"
#include "portable/portmacro.h"
#include "semphr.h"
#include "avr/pgmspace.h"
#include "arduinoFFT.h"
#include "core_pins.h"
#include "projdefs.h"
#include "wiring.h"
#include <WS2812Serial.h>

#include "goertzel.h"

#include <Arduino.h>
#include <vector>
#include <cmath>
#include <complex>

#define ever (;;)

/******************************************************************************
 * Config
 ******************************************************************************/

#define INTENSE_RED    0x990000
#define INTENSE_GREEN  0x009900
#define INTENSE_BLUE   0x000099
#define INTENSE_YELLOW 0x999900
#define INTENSE_PINK   0x991088
#define INTENSE_ORANGE 0xE05800
#define INTENSE_WHITE  0x999999

// Less intense...
#define RED    0x160000
#define GREEN  0x001600
#define BLUE   0x000016
#define YELLOW 0x101400
#define PINK   0x120009
#define ORANGE 0x100600
#define PURPLE 0x100020
#define WHITE  0x101010
#define OFF    0x000000

#define GOLD   0xAE8625
#define SILVER   0xC0C0C0

const uint32_t cooldown_choices_ms[] = {3'000, 7'000, 12'000};
static volatile uint32_t cooldown_ms = cooldown_choices_ms[1];
int plr_clrs_lock[2] = {INTENSE_RED, INTENSE_BLUE};
/*int plr_clrs_lock[2] = {GOLD, SILVER};*/
/*int plr_clrs_unlock[2] = {RED, BLUE};*/
/*int plr_clrs_unlock[2] = {ORANGE, ORANGE};*/
int plr_clrs_unlock[2] = {PINK, PINK};

// Threshold for ewma of goertzel filter before considered touching
// Not sure if goertzel filter isn't scale invariant to e.g. window size,
// freq, etc. If not should probably be scaled appropriately but I'm too lazy
const float goertzel_thresh = 10;
// How long of a period to compute goertzel filter for
const float goertzel_win_ms = 100;

// Grace time after picking up piece before assuming placed back in same spot
const float debounce_ms = 500;

const bool upside_down_mode = false;

/******************************************************************************
 * Structs
 ******************************************************************************/
typedef struct coord_t {
  int32_t rank;
  int32_t file;
  float x_cm = 0;
  float y_cm = 0;
} coord_t;

/******************************************************************************
 * FFT/Detection
 ******************************************************************************/
const float freq_sample = 1500; //Hz, must be less than 10000 due to ADC
double freq_output[2] = { 500, 600 };

/******************************************************************************
 * Hardware Definitions
 ******************************************************************************/
// All taken from kicad schematic
const int n_sqr = 16;

int em_pins[n_sqr] = {
  4, 5, 6, 7,
  8, 9, 10, 11,
  12, 40, 41, 30,
  31, 32, 33, 36,
};

/* int em_pins[n_sqr] = { */
/*     4, 5, 6, 7, */
/*     8, 9, 10, 11, */
/*     0, 40, 41, 30, */
/*     31, 32, 33, 36, */
/* }; */

int sens_pins[n_sqr] = {
  14, 15, 16, 17,
  18, 19, 20, 21,
  22, 23, 24, 25,
  26, 27, 38, 39,
};

const float square_cm = 5.0;
const float square_center_to_led_cm = 1.8;
const coord_t coord_center = {
  .rank = -1,
  .file = -1,
  .x_cm = 4 * square_cm,
  .y_cm = 4 * square_cm,
};

int freq_pin = 2;

const int led_pin = 1;

int jmp_pins[2] = { 37, 3 };

/*
 * Note: these are opposite to the definitions in the hardware design
 * This is because how I hooked up the pcbs physically happened to be opposite
 * to what I originally planned
 */
HardwareSerialIMXRT &serial_prev = Serial8;
HardwareSerialIMXRT &serial_next = Serial7;

/******************************************************************************
 * ws2812Serial
 ******************************************************************************/
const int num_leds = 128;

byte drawingMemory[num_leds*3];         //  3 bytes per LED
DMAMEM byte displayMemory[num_leds*12]; // 12 bytes per LED

WS2812Serial leds(num_leds, displayMemory, drawingMemory, led_pin, WS2812_GRB);
SemaphoreHandle_t leds_mut;

/******************************************************************************
 * FreeRTOS
 ******************************************************************************/

#define n_cooldown_change (1 << 0)

// Hacky, but arbitrary large negative ticks so don't have to wait at beginning
int neg_tick = -pdMS_TO_TICKS(10'000);

// Semaphores
SemaphoreHandle_t adc_mut;

// Task handles
TaskHandle_t serial_handle;

/******************************************************************************
 * Inter board communication
 ******************************************************************************/

enum board_msg {
  m_cooldown_change = 'c', // format: "cX\n", X is binary encoded cooldown in ms
};

/******************************************************************************
 * Global variables
 ******************************************************************************/

// Which board this is, 0 is top left and increases counter clockwise
static unsigned int board_id;
static volatile int cooldown_selection = 1;

extern const uint32_t num_frames;
extern const float frame_rate;
extern const uint32_t frames[1000][8][8][8];

typedef enum board_mode_t {
  PLAY,
  INTRO,
  VIDEO,
  SETTINGS,
} board_mode_t;

static volatile board_mode_t board_mode = INTRO;

/******************************************************************************
 * Helper functions
 ******************************************************************************/

// idx is index of square on board, i is pixel
// i=-1 => center of square
coord_t idx_to_coord(uint32_t idx, int32_t i = -1){
  coord_t ret;
  float dx = 0, dy = 0;
  if(i != -1){
    float led_theta = i * 2.0 * PI / 8.0;
    dx = -square_center_to_led_cm * cos(led_theta);
    dy = -square_center_to_led_cm * sin(led_theta);
  }
  float old_dx = dx;
  switch(board_id) {
    case 0:
      ret.rank = (idx % 4) + 4;
      ret.file = idx / 4;
      break;
    case 1:
      ret.rank = (idx / 4);
      ret.file = 3 - (idx % 4);
      dx = -dy;
      dy = old_dx;
      break;
    case 2:
      ret.rank = 3 - (idx % 4);
      ret.file = 7 - (idx / 4);
      dx = - dx;
      dy = -dy;
      break;
    case 3:
      ret.rank = 7 - (idx / 4);
      ret.file = 4 + (idx % 4);
      dx = dy;
      dy = -old_dx;
      break;
  }
  ret.x_cm = ret.file * square_cm + dx + square_cm / 2.0;
  ret.y_cm = ret.rank * square_cm + dy + square_cm / 2.0;

  /*if(ret.file == ret.rank && i == 0){*/
  /*    float led_theta = i * 2.0 * PI / 8.0;*/
  /*    dx = -square_center_to_led_cm * cos(led_theta);*/
  /*    dy = -square_center_to_led_cm * sin(led_theta);*/
  /*    Serial.print("dx: ");*/
  /*    Serial.print(dx);*/
  /*    Serial.print(", dy: ");*/
  /*    Serial.print(dy);*/
  /*    Serial.println();*/
  /*}*/

  return ret;
}

uint32_t change_intensity(uint32_t col, float mult){
  uint32_t red = ((col >> 16) & 0xFF) * mult;
  uint32_t green = ((col >> 8) & 0xFF) * mult;
  uint32_t blue = (col & 0xFF) * mult;
  return (red << 16) | (green << 8) | blue;
}

uint32_t norm_intensity(uint32_t col, float norm){
  uint32_t r = ((col >> 16) & 0xFF);
  uint32_t g = ((col >> 8) & 0xFF);
  uint32_t b = (col & 0xFF);
  float brightness = 0.2126 * r + 0.7152 * g + 0.0722 * b;
  float mult = norm / max(1, brightness);
  r *= mult;
  g *= mult;
  b *= mult;
  float gamma = 2.2;
  r = int(pow(r / 255.0, gamma) * 255);
  g = int(pow(g / 255.0, gamma) * 255);
  b = int(pow(b / 255.0, gamma) * 255);
  return (r << 16) | (g << 8) | b;
}

uint32_t hsv_to_rgb(float h, float s, float v, float fade) {
  float r, g, b;

  int i = (int)(h * 6);
  float f = h * 6 - i;
  float p = v * (1 - s);
  float q = v * (1 - f * s);
  float t = v * (1 - (1 - f) * s);

  switch (i % 6) {
    case 0: r = v, g = t, b = p; break;
    case 1: r = q, g = v, b = p; break;
    case 2: r = p, g = v, b = t; break;
    case 3: r = p, g = q, b = v; break;
    case 4: r = t, g = p, b = v; break;
    default:
    case 5: r = v, g = p, b = q; break;
  }
  float reduction = 0.25 * fade;
  r *= reduction;
  g *= reduction;
  b *= reduction;

  return ((int)(r * 255) << 16) | ((int)(g * 255) << 8) | (int)(b * 255);
}

uint32_t get_rainbow_color(float h, float fade) {
  /*float h = (step % 360) / 360.0;  // Cycle hue between 0 and 1*/
  float s = 1.0;                   // Full saturation
  float v = 0.3;                   // Adjust brightness here (0 to 1)

  return hsv_to_rgb(h, s, v, fade);
}

void color_wipe(int color, int wait_ms) {
  for (int i=0; i < leds.numPixels(); i++) {
    leds.setPixel(i, color);
    leds.show();
    vTaskDelay(pdMS_TO_TICKS(wait_ms));
  }
}

void color_spiral(int idx, int step, int max_step){

  for(int i = 0; i < 8; ++i){
    coord_t coord = idx_to_coord(idx, i);

    float theta = atan2(coord.y_cm - coord_center.y_cm, coord.x_cm - coord_center.x_cm);// + 1.5 * PI;
    float time_adjust = (atan((step-max_step/2.0)*2/max_step * 3)-atan(-3))*max_step/500;
    float fade = min(1.0, 4.0*(max_step-step)/max_step);
    leds.setPixel(8*idx + i, get_rainbow_color(fmod(theta / 2.0 / PI + time_adjust + 1000, 1), fade));

    /*if(coord.file == 0 && coord.rank == 3){*/
    /*    Serial.print("file: ");*/
    /*    Serial.print(coord.file);*/
    /*    Serial.print(", rank: ");*/
    /*    Serial.print(coord.rank);*/
    /*    Serial.print(", i:");*/
    /*    Serial.print(i);*/
    /*    Serial.print(", x_cm: ");*/
    /*    Serial.print(coord.x_cm);*/
    /*    Serial.print(", y_cm: ");*/
    /*    Serial.print(coord.y_cm);*/
    /*    Serial.print(", ");*/
    /*    Serial.print(theta);*/
    /*    Serial.print(", ");*/
    /*    Serial.println(((unsigned int)(180.0/PI*theta / 3.0 + 1000 + 45) % 180) / 180.0);*/
    /*}*/
  }

}

void play_video(int idx, int frame){
  /*frame = min(frame, num_frames-1);*/
  frame = frame % num_frames;
  for(int i = 0; i < 8; ++i){
    coord_t coord = idx_to_coord(idx, i);

    leds.setPixel(8*idx + i, norm_intensity(frames[frame][coord.file][coord.rank][i], 60));
  }
}

double calculate_ewma(double previous_ewma, double new_value, double alpha) {
  return alpha * new_value + (1 - alpha) * previous_ewma;
}

/******************************************************************************
 * Tasks
 ******************************************************************************/

static void blink_task(void*) {
  pinMode(arduino::LED_BUILTIN, arduino::OUTPUT);
  pinMode(jmp_pins[0], arduino::INPUT_PULLUP);
  pinMode(jmp_pins[1], arduino::INPUT_PULLUP);
  while (true) {
    digitalWriteFast(arduino::LED_BUILTIN, arduino::LOW);
    vTaskDelay(pdMS_TO_TICKS(500));

    digitalWriteFast(arduino::LED_BUILTIN, arduino::HIGH);
    vTaskDelay(pdMS_TO_TICKS(500));
    /*Serial.println(board_id);*/
    /*Serial.print("JMP 1: ");*/
    /*Serial.println(digitalRead(jmp_pins[0]));*/
    /*Serial.print("JMP 2: ");*/
    /*Serial.println(digitalRead(jmp_pins[1]));*/
  }
}

static void led_task(void*) {
  for ever {
    if(xSemaphoreTake(leds_mut, pdMS_TO_TICKS(20))){
      /*leds.setPixel(0, WHITE);*/
      leds.show();
      xSemaphoreGive(leds_mut);
    } else {
      Serial.println("LED mutex failed!");
    }
    vTaskDelay(pdMS_TO_TICKS(50));
  }
}

static void square_task(void *params) {
  int idx = *((int*) params);
  unsigned int sampling_period_us = round(1000000*(1.0/freq_sample));

  pinMode(em_pins[idx], arduino::OUTPUT);
  digitalWrite(em_pins[idx], 0);

  // Test sequence
  /*for (int i=0; i < 8; i++) {*/
  /*    leds.setPixel(8*idx + i, WHITE);*/
  /*}*/
  /*for ever {}*/

  TickType_t last_print = xTaskGetTickCount();
  TickType_t last_led = xTaskGetTickCount();
  TickType_t last_wake = xTaskGetTickCount();

  unsigned int freq_ewma[2] = { 0, 0 };
  int last_touching[2] = { neg_tick, neg_tick };

  // Representation invariant: cooldown_start > 0 => last_plr != -1
  TickType_t cooldown_start = neg_tick;
  int last_plr = -1; // -1 for empty square
  coord_t coord = idx_to_coord(idx);
  if(coord.rank <= 1)
    last_plr = 0;
  else if(coord.rank >= 6)
    last_plr = 1;
  /* if((coord.rank == 0 || coord.rank == 7) && (coord.file == 0 || coord.file == 7)) */
  /*     last_plr = 0; */


  unsigned int goertzel_win_samples = goertzel_win_ms * freq_sample / 1000;
  Goertzel goertzels[2] = { Goertzel(freq_output[0], freq_sample, goertzel_win_samples), Goertzel(freq_output[1], freq_sample, goertzel_win_samples) };


  // Loading screen
  TickType_t t_init = xTaskGetTickCount();
  int step = 0;
  int intro_delay_ms = 10;
  int intro_ms = 10'000;
  /* int intro_ms = 10'000; */
  /*int intro_ms = 100000'000;*/
  int ui_ms = 10'000'000;


  // Main task
  for ever {
    TickType_t cur_tk = xTaskGetTickCount();

    bool on_cooldown = cur_tk - cooldown_start <= pdMS_TO_TICKS(cooldown_ms);

    // Only activate ems if on cooldown
    if(on_cooldown || (upside_down_mode && last_plr != -1)){
      digitalWrite(em_pins[idx], 1);
    } else {
      digitalWrite(em_pins[idx], 0);
    }

    // Sample adc
    float sample = 0;
    if(xSemaphoreTake(adc_mut, pdMS_TO_TICKS(100))){
      sample = analogRead(sens_pins[idx])*3.3/1024;
      xSemaphoreGive(adc_mut);
    }

    for(int p = 0; p < 2; ++p){
      // Update goertzel/ewma
      goertzels[p].addSample(sample);
      freq_ewma[p] = calculate_ewma(freq_ewma[p], goertzels[p].getMagnitude(), 0.3);

      // Whether been touched by this plr recently
      bool prev_touching = cur_tk - last_touching[p] < pdMS_TO_TICKS(debounce_ms);

      // Make sure to check that this frequency is actually dominant, as there
      // can be overlap
      if(freq_ewma[p] >= goertzel_thresh && freq_ewma[p] > freq_ewma[!p]){
        switch(board_mode) {
          case INTRO:
          case VIDEO:
            board_mode = PLAY;
            break;
          case PLAY:
            {
              // New touch from empty
              if(last_plr == -1 && !prev_touching){
                last_plr = p;
                cooldown_start = cur_tk;
                // Reset square
              } else if(last_plr == p && !on_cooldown){
                last_plr = -1;
                // Override square (for capture)
              } else if(last_plr == !p){
                last_plr = -1;
                cooldown_start = neg_tick;
              }
            }
            break;
          case SETTINGS:
            break;
        }

        last_touching[p] = cur_tk;
      }
    }

    /* if(cur_tk - last_print >= pdMS_TO_TICKS(500) && (idx == 10 || idx == 11)){ */
    /*     Serial.print(idx); */
    /*     Serial.print(", "); */
    /*     Serial.print(goertzels[0].getMagnitude()); */
    /*     Serial.print(", "); */
    /*     Serial.print(goertzels[1].getMagnitude()); */
    /*     Serial.print(", "); */
    /*     Serial.println(sample); */
    /*     last_print = cur_tk; */
    /* } */


    switch(board_mode) {
      case PLAY:
      {
        if(cur_tk - last_led >= pdMS_TO_TICKS(50)){
          if(xSemaphoreTake(leds_mut, pdMS_TO_TICKS(100))){
            int p = last_plr;
            for (int i=0; i < 8; i++) {
              // Cooldown is bright
              if(on_cooldown){
                float fraction_through = (cur_tk - cooldown_start) * 1. /pdMS_TO_TICKS(cooldown_ms);
                float min_intensity = 0.05;
                if(i == (int) (fraction_through * 8)){
                  /*float intensity_modifier = (1-(fraction_through - i / 8.) * 8) * (1 - min_intensity) + min_intensity;*/
                  float intensity_modifier = (1-(fraction_through - i / 8.) * 8) * (1 - min_intensity) + min_intensity;
                  leds.setPixel(8*idx + i, change_intensity(plr_clrs_lock[p], intensity_modifier));
                }else if( i > (int) (fraction_through * 8)){
                  leds.setPixel(8*idx + i, plr_clrs_lock[p]);
                } else {
                  leds.setPixel(8*idx + i, change_intensity(plr_clrs_lock[p], min_intensity));
                }
              } else if(last_plr != -1){
                leds.setPixel(8*idx + i, plr_clrs_unlock[p]);
              } else {
                leds.setPixel(8*idx + i, OFF);
              }
              /*leds.setPixel(8*idx + i, WHITE);*/
            }
            xSemaphoreGive(leds_mut);
          } else Serial.println("Failed to take led mutex!");
          last_led = cur_tk;
        }
        break;
      }
      case SETTINGS:
        break;
      case VIDEO:
        break;
      case INTRO:
      {
        if(xTaskGetTickCount() - last_wake > pdMS_TO_TICKS(intro_delay_ms)){
          leds.setPixel(8*idx + 0, WHITE);
          /* color_spiral(idx, step, intro_ms/intro_delay_ms); */
          /* play_video(idx, (int)(pdTICKS_TO_MS(xTaskGetTickCount() - t_init) / 1000.0 * frame_rate)); */
          ++step;
          last_wake = xTaskGetTickCount();
        }
        if(xTaskGetTickCount() - t_init > pdMS_TO_TICKS(intro_ms)){
          board_mode = PLAY;
        }
        break;
      }
    }


    // Read cooldown interface
    /*if(board_id == 0 && cur_tk - t_init < pdMS_TO_TICKS(intro_ms + ui_ms)){*/
    /*    int clrs[] = {RED, YELLOW, GREEN, WHITE};*/
    /*    int clrs_intense[] = {INTENSE_RED, INTENSE_YELLOW, INTENSE_GREEN, INTENSE_WHITE};*/
    /**/
    /*    bool cur_touching = last_touching[0] == (int)cur_tk || last_touching[1] == (int)cur_tk;*/
    /**/
    /*    if(idx % 4 == 0){*/
    /*        int i = idx/4;*/
    /*        // No cooldown if ui button*/
    /*        cooldown_start = neg_tick;*/
    /*        if(cur_touching && i < 3){*/
    /*            cooldown_selection = i;*/
    /*            cooldown_ms = cooldown_choices_ms[i];*/
    /*            xTaskNotify(serial_handle, n_cooldown_change, eSetBits);*/
    /*        }*/
    /*        if(xSemaphoreTake(leds_mut, pdMS_TO_TICKS(100))){*/
    /*            for(int j = 0; j < 8; ++j){*/
    /*                leds.setPixel(8*idx + j, cooldown_selection == i ? clrs_intense[i] : clrs[i]);*/
    /*            }*/
    /*            xSemaphoreGive(leds_mut);*/
    /*        } else Serial.println("Failed to take led mutex!");*/
    /*    }*/
    /*}*/


    if(!xTaskDelayUntil(&last_wake, pdUS_TO_TICKS(sampling_period_us))){
      // This actually gets called pretty often if you try playing around with sample rate/tick rate
      // (=>) Worth keeping an eye on the serial monitor if detection isn't working
      Serial.println("Square task not actually delayed (computation/adc reads probably taking too long)");
    }
  }
}

static void freq_output_task(void *params) {
  int idx = *((int*) params);

  TickType_t last_wake = xTaskGetTickCount();
  uint8_t output_state = 0;

  pinMode(freq_pin, arduino::OUTPUT);

  for ever {
    output_state = !output_state;
    digitalWrite(freq_pin, output_state);
    vTaskDelayUntil(&last_wake, pdUS_TO_TICKS(1e6/freq_output[idx]/2));
  }
}

static void serial_task(void *params) {
  (void) params;

  char prev_msg[100];
  uint32_t prev_msg_len = 0;

  for ever {
    // Check for notifications
    uint32_t notification;
    if(xTaskNotifyWait(0, 0xFFFFFFFF, &notification, 0)){
      Serial.println("Got notification!");
      if(notification & n_cooldown_change){
        Serial.println("Cooldown notification!");
        serial_next.write(m_cooldown_change);
        serial_next.write((cooldown_ms >> 24) & 0xFF);
        serial_next.write((cooldown_ms >> 16) & 0xFF);
        serial_next.write((cooldown_ms >> 8) & 0xFF);
        serial_next.write(cooldown_ms & 0xFF); 
        serial_next.println();
      }
    }
    if(board_id == 0){
      /*serial_next.println("Hello world");*/
    } else {
      // Forward message
      while(serial_prev.available()){
        unsigned char in_byte = serial_prev.read();
        serial_next.write(in_byte);

        if(prev_msg_len + 1 < sizeof prev_msg / sizeof prev_msg[0])
          prev_msg[prev_msg_len++] = in_byte;

        if(in_byte == '\n'){
          switch(prev_msg[0]) {
            case m_cooldown_change:
              Serial.println("Changing cooldown");
              if(prev_msg_len >= 5)
                cooldown_ms = prev_msg[1] << 24 |
                  prev_msg[2] << 16 |
                  prev_msg[3] << 8 |
                  prev_msg[4];
              break;
            default:
              break;
          }
          prev_msg_len = 0;
        }
        Serial.write(in_byte);
      }
    }
    vTaskDelay(pdMS_TO_TICKS(20));
  }
}

/******************************************************************************
 * Arduino Setup/Loop
 ******************************************************************************/
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
void loop() {}

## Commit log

2024-04-07 Added electromagnet driver circuit
2024-04-28 Started pcb
    [kfchess.kicad_pcb, kfchess.kicad_sch, leds.kicad_sch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]
2024-06-08 Fixed holes
    [kfchess.kicad_pcb]
2024-06-08 Started routing
    [kfchess.kicad_pcb, kfchess.kicad_sch, row.kicad_sch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]
2024-06-09 More routing
    [kfchess.kicad_pcb, square.kicad_sch]
2024-06-09 Finished routing top squares
    [kfchess.kicad_pcb]
2024-06-10 Actually finished top
    [kfchess.kicad_pcb]
2024-06-10 Copied routing for bottom squares
    [kfchess.kicad_pcb, kfchess.kicad_sch]
2024-06-10 Tentatively finished routing
    [kfchess.kicad_pcb]
2024-06-10 Fixed errors
    [kfchess.kicad_pcb]
2024-06-17 Got ws2812 leds working
    [kfchess.kicad_pcb]
2024-06-18 Reorganized directories
    [kfchess.kicad_pcb, kfchess.kicad_sch, leds.kicad_sch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]
2024-06-19 Combined led and fft tasks
2024-06-19 Fixed mutex issues with adc
    [main.cpp]
2024-06-19 Added second goertzel filter
2024-06-19 Added timeout to led mutex
2024-07-01 Switched to new board shape
    [kfchess.kicad_pcb]
2024-07-02 New layout
    [kfchess.kicad_pcb, kfchess.kicad_sch, row.kicad_sch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]
2024-07-04 Finished layout
    [kfchess.kicad_pcb, kfchess.kicad_sch, row.kicad_sch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]
2024-07-04 Finished routing
    [kfchess.kicad_pcb]
2024-07-04 Went through and fixed drc
    [kfchess.kicad_pcb]
2024-07-04 Added edge pcbs
    [edge1.kicad_pcb, edge1.kicad_sch, kfchess.kicad_pcb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]
2024-07-04 Added logo to edge4
    [edge1.kicad_pcb]
2024-07-04 Fixed upside down cross board screw terminals
    [edge1.kicad_pcb, kfchess.kicad_pcb, kfchess.kicad_sch]
